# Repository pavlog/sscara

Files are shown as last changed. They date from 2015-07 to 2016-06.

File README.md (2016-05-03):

# sscara
Small size 3d printer with SCARA based mechanics

Current Status: V3 - DONE

V3 Videos:
https://youtu.be/qMoxgC5KaG4
https://youtu.be/IasEUXix5cc
https://youtu.be/JhraS_r1Fzk

History:
* 01.05.2016 - V3 - DONE
* 28.01.2016 - V3 - WIP
* 11.01.2016 - V2 - DONE (fail)
* 05.01.2016 - V2 - Final tests
* 28.07.2015 - V2 - WIP
* 27.07.2015 - V1 - DONE
* 27.04.2015 - V1 - WIP

Precision:
WIP
XY: 0.03 mm with 32 microsteps at 150 mm radius from axes center. (chord length c=2*R*sin(alpha/2), alpha = 1.8/5/32 (stepper/gearratio/nummicrosteps);
Z: GT2 16 teeth pulley with 32 microsteps - 5 μm (http://reprap.org/wiki/Step_rates)
 
Other features:
* Noiseless

Hardware: 
* 4 Nema17 (24mm length shaft)
* Ramps 1.4
* 4 drv8825 (drv8825 is better due to 1/32 microstepping)
* External power supply 5A (without Heated bed)
* Heated bed ????? depends on (but seems like require in 4x time less current than MK2B - because of 4 times lower area)
* 3 small (20x11x7mm) end stoppers
Optional:
* HC-05 bluetooth module (i am happy with it, even firmware flashing done via bluetooth)

Marlin Firmware modifications:
* FIVE_BAR define added for SCARA define
* added M450 - xyz min limits
* added M451 - xyz max limits
* added M452 - xyz home pos
* added M370 X#Angle Y#Angle
* G2/G3 commands support
* Fixed math for pure SCARA (2 arms)

Materials:
* ~1.5 meters(2m max) - GT2 timing belt 6mm(width)
* 3 - GT2 16 teeth pulleys (ID=5mm)
* 4 - Nema17 (24mm shaft length) (39 mm Nema17 might be used for xy)
* 4 - 625 bearings (ID-5mm,OD-16mm,H-5mm)
* 2 - 608 bearings (ID-8mm,OD-22mm,H-7mm)
* 21 - 623 bearings (ID-3mm,OD-10mm,H-4mm)
* 1 - aluminium tube (ID-6mm,OD-8mm) - 350mm max
* 1 - m5 threaded rod - 500mm max
* 1 - m3 threaded rod - 2 meters max
* m3 bolts and nuts
* m5 nuts
* ABS filament to print parts

SCAD:
* use drawArray = [] to draw everything or drawArray=[1,2,3] for parts
* use printLayout to control parts/subparts layout (0 for design, 1 for export) (Some parts need to be rotated to 180 Y) (WIP)
* NemaSize - tweak nema len, NemaLengthMedium,NemaLengthShort,NemaLengthLong

Slicer:
* Slic3r
* ABS - 0.4mm nozzle, setup is described in scad file for each part

Included Software:
* Software/SScaraVisualizer.html (may not be up to date) or use (up to date) https://jsfiddle.net/PavloG/0vq1nf2v/
* Marlin firmware - use https://github.com/pavlog/Marlin (forked from https://github.com/MarlinFirmware/Marlin)

Reachability visualizer
* http://jsfiddle.net/PavloG/0vq1nf2v/

Calibration Guide:
Enable EEPROM in you firmware.

Initial rough calibration:
* G28 goto home
* Steps Per Units - M92 X## Y## where ## is a stepperUnitsPerRevolution*driverMicrostepping*gearboxration/360, (Nema17 1.8deg with drv8825 1/32), v1 = 200*32*5/360 = 88.888, v2 = 142.222

XY init calibration:

* G28 goto home
* M452 X#xx Y#yy - where #xx and #yy is a measured distance from nozzle to the axis center (xx should negative, +/-1 mm is enought)

NOTE: Put your min max software limits a little bit bigger (i used 3 cm)  (use M450 and M451), this is required for the next steps.

XY precise calibration:

Precise Steps Per Units calibration:
* G28 goto home
* M370 X0+#xx Y-90+#yy // move arms to 90 and 180 degrees, #xx and #yy is an extra angle to move arms exactly to 90 and 180 degrees
* M370 X90+#xx Y0+#yy // #xx and #yy from prev step
* if your arms not exacly 0 and 90 degrees use M92 X## Y## +/- values until all sequence above will get 0 and 90 degrees
* Repeat a few times until you get 90 and 180 degrees exactly
* M500 to save data to EEPROM

Precise home offsets calibration:
* G28 goto home
* M370 X0 Y-90 // move arms to 0 and -90 degrees
* M206 X## Y## (where X## Y## is a angular distance to 90 and 180, this is homing offsets in angles, can be used from prev steps)
* Repeat a few times until you get 90 and 180 degrees exactly
* M500 to save data to EEPROM

Z calibration
* G28 Z
* Ajust platform height

Development blog - https://3dgems.blogspot.com

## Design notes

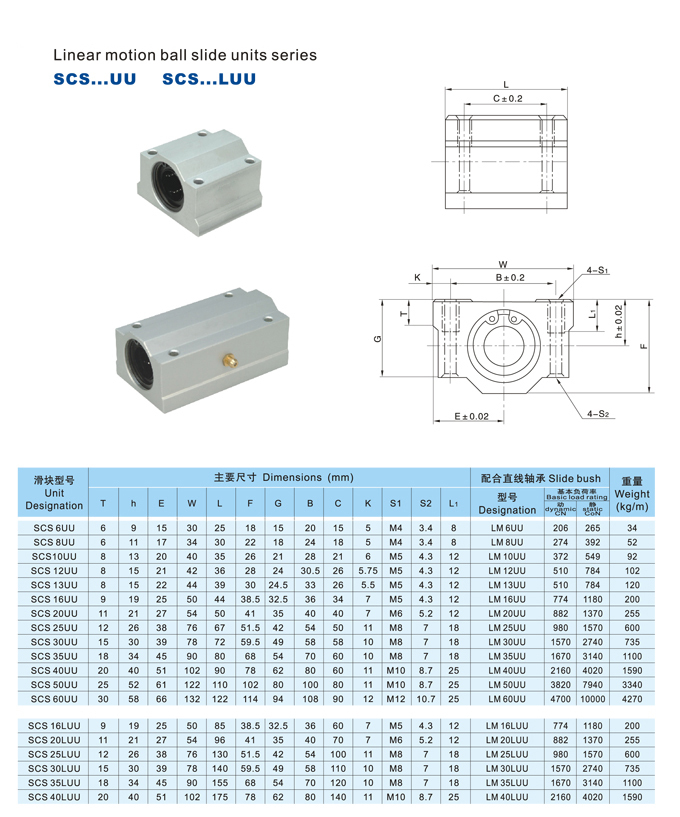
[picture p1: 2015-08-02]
Modules/scs_uu.png

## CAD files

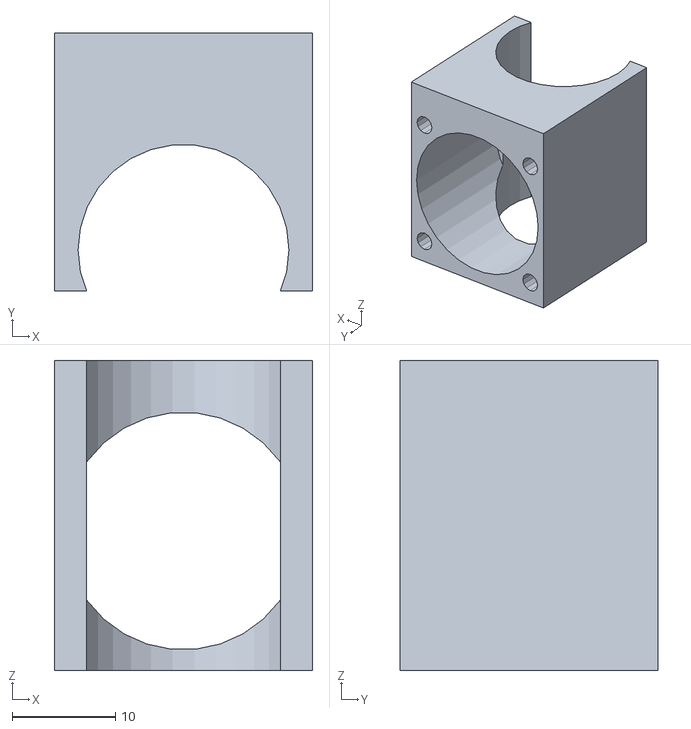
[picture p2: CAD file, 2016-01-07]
Misc/25MMFAN.stl
25.0 x 25.0 x 30.0

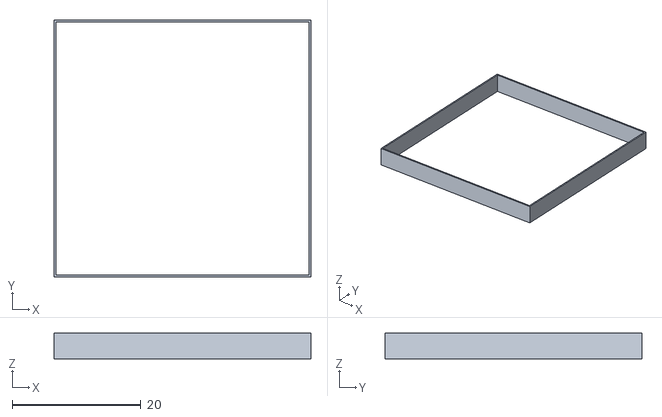
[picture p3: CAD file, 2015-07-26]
STL/CalibrationTests/CalibrationTests40X40.stl
40.0 x 40.0 x 4.00

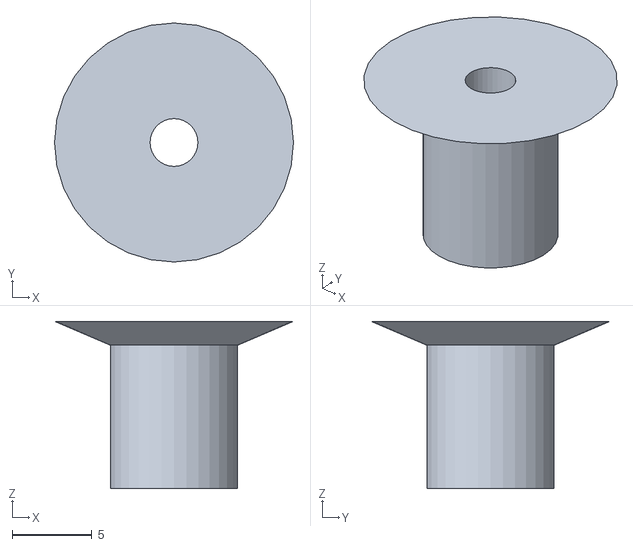
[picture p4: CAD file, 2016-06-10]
STL/V3/part_13_extruder_hinge_stick.stl
15.0 x 15.0 x 10.5

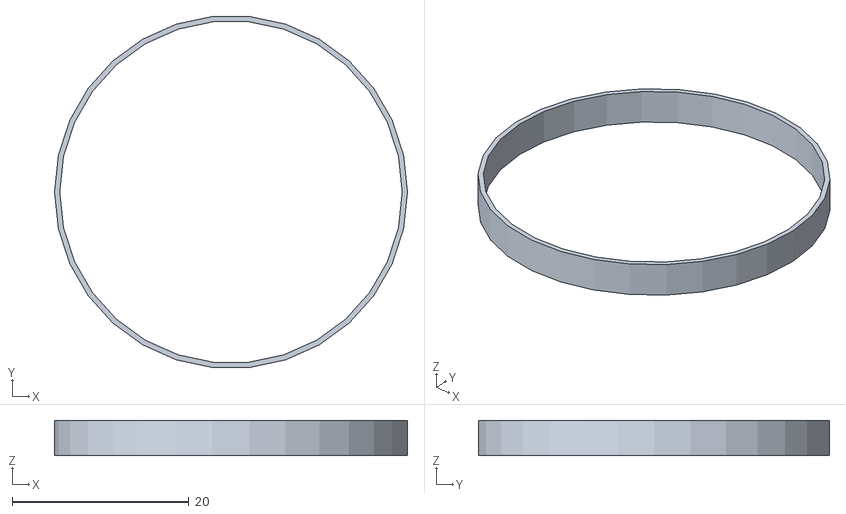
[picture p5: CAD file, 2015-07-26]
STL/CalibrationTests/CalibrationTests_circle.stl
40.0 x 39.8 x 4.00

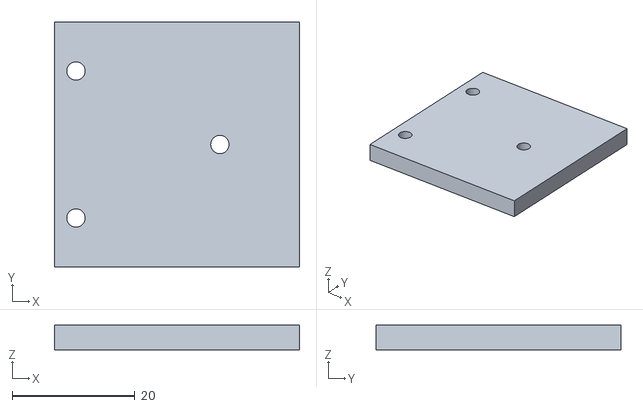
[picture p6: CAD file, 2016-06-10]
STL/V3/part_14_extruder_hinge_plate.stl
40.0 x 40.0 x 4.00

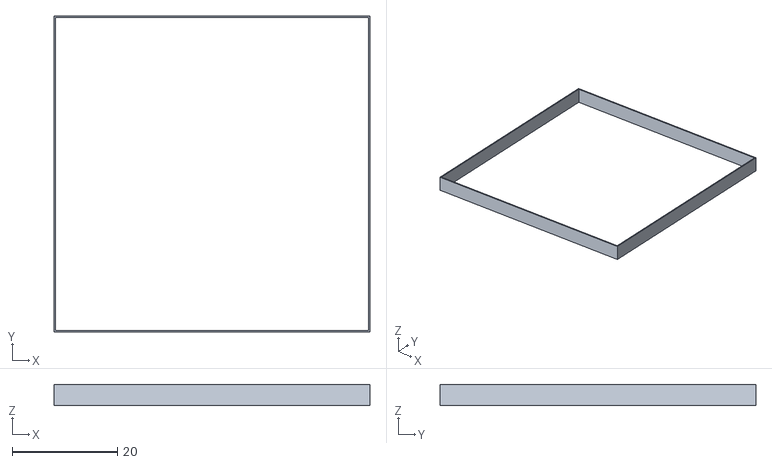
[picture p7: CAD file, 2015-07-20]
STL/CalibrationTests/CalibrationTests60X60.stl
60.0 x 60.0 x 4.00

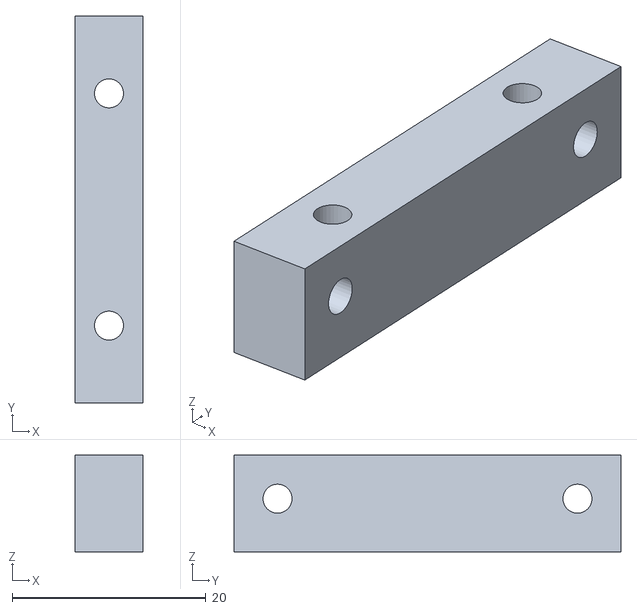
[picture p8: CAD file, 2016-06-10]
STL/V3/part_15_extruder_stepper_mount.stl
7.00 x 40.0 x 10.0

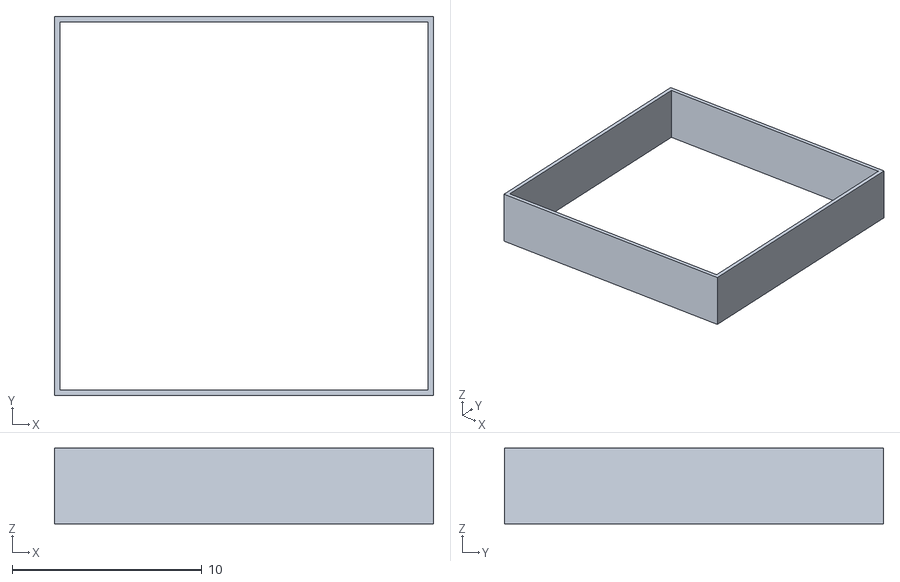
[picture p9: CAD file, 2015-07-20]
STL/CalibrationTests/CalibrationTests.stl
20.0 x 20.0 x 4.00

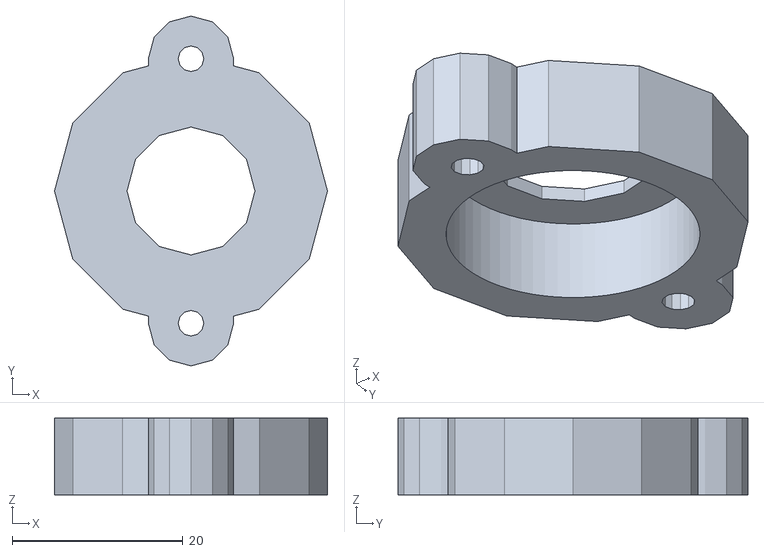
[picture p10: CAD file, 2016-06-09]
STL/V3/part_12_extruder_hinge_mount.stl
32.0 x 41.0 x 9.00

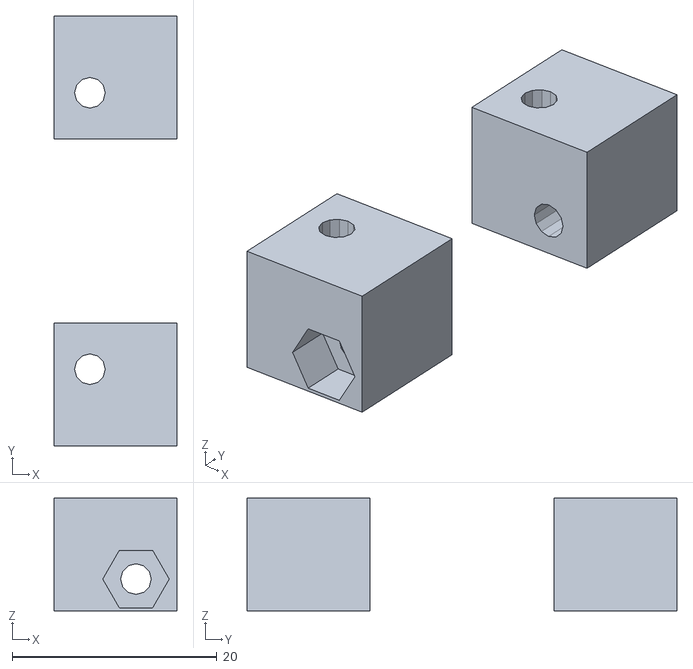
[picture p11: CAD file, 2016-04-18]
STL/V3/topFrontMounts.stl
12.0 x 42.0 x 11.0

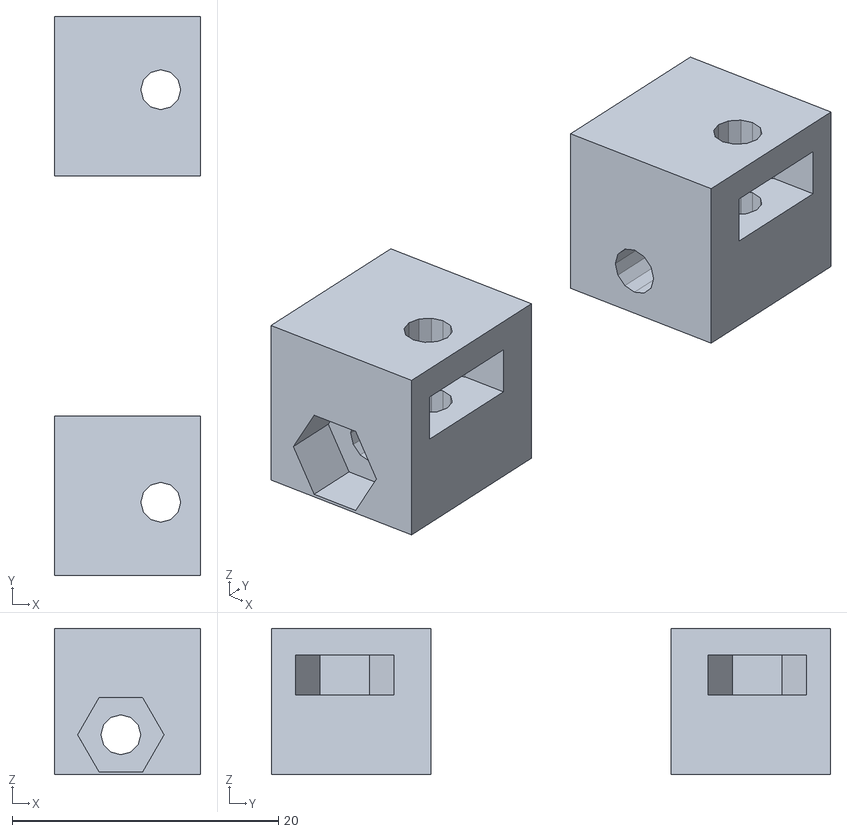
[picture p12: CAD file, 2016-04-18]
STL/V3/topMiddleMounts.stl
11.0 x 42.0 x 11.0

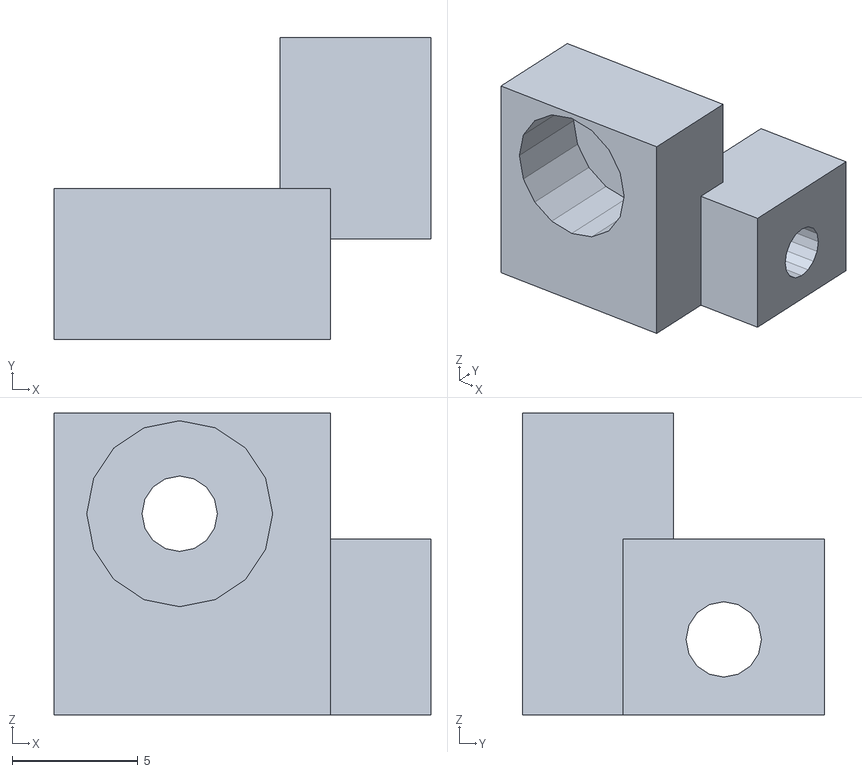
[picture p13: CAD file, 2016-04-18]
STL/V3/part_10_subpart2.stl
15.0 x 12.0 x 12.0

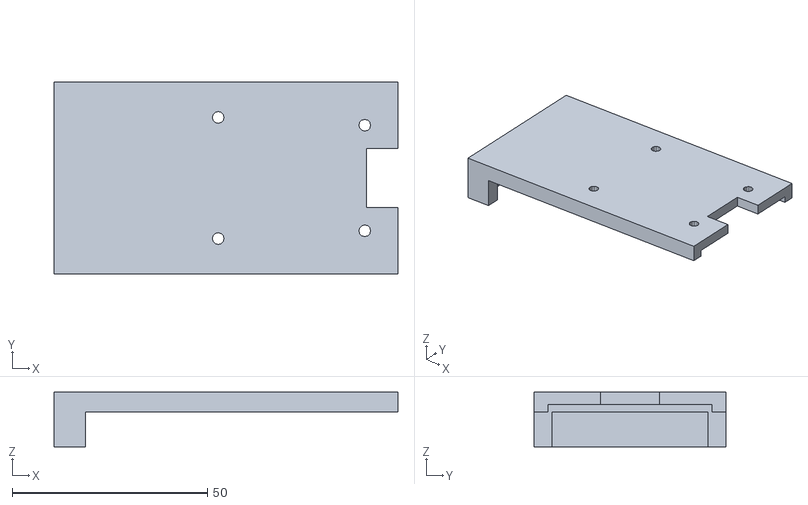
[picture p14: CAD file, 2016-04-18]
STL/V3/topCap.stl
88.0 x 49.0 x 14.0

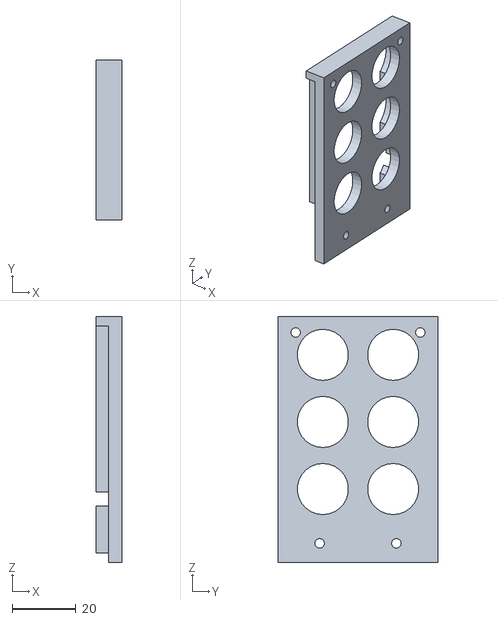
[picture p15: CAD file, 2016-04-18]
STL/V3/part_10_subpart1.stl
8.00 x 50.0 x 77.0

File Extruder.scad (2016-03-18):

// Author: Pavlo Gryb (psg416@gmail.com)

use <Modules/Pulley_T-MXL-XL-HTD-GT2_N-tooth.scad>
use <Modules/ISOThread.scad>
use <Modules/Bearings.scad>
use <Modules/EndStoppers.scad>
use <Modules/Write.scad/Write.scad>
include <Modules/MCAD/stepper.scad>
use <Modules/HotEnds.scad>
use <Modules/LCD.scad>
use <Modules/Misc.scad>
use <Modules/Profiles.scad>
use <Modules/RAMPS.scad>
include <Modules/dimlines.scad>
include <Modules/TextGenerator.scad>

gearRadToTeethEnd = 10.0/2;//7.3/2;// seems like mk8
gearRad = 11.5/2;// semms like mk8
fillamentD = 1.75;
fillamentPenetration = 0.5;//mm
extruderBearingDia = Bearing623Diameter();
extruderBearingH = Bearing623Height();
extruderClearanceH = 0.2;

printLayout = 0;

module ExtruderStepperPanel()
{
					hull()
				{
					translate([-14,-14,0]) cylinder(r=7.2,h=4,$fn=32);
					translate([14,-14,0]) cylinder(r=7.2,h=4,$fn=32);
					translate([14,14,0]) cylinder(r=7.2,h=4,$fn=32);
					translate([-14,14,0]) cylinder(r=7.2,h=4,$fn=32);
					//translate([24.5+extrudeMountZOffset,9,0]) cylinder(r=7.5,h=4);
				}

}

// extruder
//if( drawArray==[] || search(11,drawArray)!=[] )
{
	//printLayout = 1;
	aY = printLayout ? 0 : 90;
	aYY = printLayout ? 180 : -90;
	armX = printLayout ? 12 :0;
	armY = printLayout ? -38 : 0;
	armZ = printLayout ? -24.75 : 0;
	armRZ = printLayout ? 196.69 : 0;
	armRX = printLayout ? 90 : 0;
	armTX = printLayout ? 10 : 0;
	translate ([0,0,0]) rotate([0,aYY,0]) rotate([0,0,aY]) mirror()//rotate([90,0,0]) 
	{
		armH = extruderBearingH+3+3;
		partsOffset = -13;
		if( !printLayout )
		{
			rotate([0,0,90]) Nema17_shaft24_Stepper();
		}
		translate([0,0,-3])
		{
			difference()
			{
				//cube([36,36,4]);
				ExtruderStepperPanel();
				extr = lookup(NemaRoundExtrusionDiameter, Nema17);
				color ("red") translate([0,0,1.5]) cylinder(d=extr+0.5,h=2.5,$fn=32);
				color ("red") translate([0,0,2]) Nema17_shaft24_Stepper(bSrewsOnly=1);
				//extruder mount
				//translate([27,10.5,-30+extrudeMountZOffset]) color("red") rotate([0,0,0]) cylinder(d=3.1,h=50,$fn=16);
				//translate([25.4,3.5,-30+extrudeMountZOffset]) color("red") rotate([0,0,0]) cylinder(d=3.1,h=50,$fn=16);
			}
			difference()
			{
				union()
				{
					color ("red")  translate([gearRadToTeethEnd-1,-12,-armH]) cube([11+3,14,armH]);
					color ("red")  translate([gearRadToTeethEnd+8,-12-1,-armH]) cube([5,3,armH]);
				}
				color( "green") translate([0,-gearRadToTeethEnd-Bearing623Diameter()/2-fillamentD/2,partsOffset+3-2]) cylinder(d=extruderBearingDia+3,h=armH+2);
				color( "green") translate([0,0,partsOffset+3-2]) cylinder(d=gearRad*2+1,h=armH+2);

				// cone
				color( "red") translate([3.9,-gearRadToTeethEnd-fillamentD/2+fillamentPenetration,-armH/2]) rotate([0,90,0]) cylinder(r2=fillamentD/2-0.2,r1=fillamentD/2+1.5,h=2,$fn=16);
				
				// fillamant
				color( "blue") translate([-50,-gearRadToTeethEnd-fillamentD/2+fillamentPenetration,-armH/2]) rotate([0,90,0]) cylinder(d=fillamentD+0.2,h=100,$fn=16);
				color( "blue") translate([10+3,-gearRadToTeethEnd-fillamentD/2+fillamentPenetration,-armH/2]) rotate([0,90,0]) cylinder(d=9,h=100,$fn=16);
				//
			}
			difference()
			{
				union()
				{
					color( "green") hull()
					{
						translate([15.5,-4-gearRadToTeethEnd-Bearing623Diameter()/2-fillamentD/2,partsOffset+3]) cylinder(d=6,h=armH+4);
						translate([20.5,-6-gearRadToTeethEnd-Bearing623Diameter()/2-fillamentD/2,partsOffset+3]) rotate([0,0,25])  cylinder(d=6,h=armH+4,$fn=16);
						translate([15.5,-5.5-gearRadToTeethEnd-Bearing623Diameter()/2-fillamentD/2,partsOffset+3]) cylinder(d=6,h=armH+4);
					}
					//color("blue") translate([25,-4.5-gearRadToTeethEnd-Bearing623Diameter()/2-fillamentD/2,partsOffset+3+4-13]) rotate([0,0,90+70])  cube([5,6.5,23]);
					//color("red") translate([26,-1.8-gearRadToTeethEnd-Bearing623Diameter()/2-fillamentD/2,partsOffset+3+4-13]) rotate([0,0,aY])  cube([5,11,10]);
					color( "green") hull()
					{
						translate([15.5,-4.5-gearRadToTeethEnd-Bearing623Diameter()/2-fillamentD/2,partsOffset+3]) cylinder(d=8,h=armH+4);
						translate([9,-1-gearRadToTeethEnd-Bearing623Diameter()/2-fillamentD/2,partsOffset+3]) cylinder(d=4.5,h=armH+4);
					}
				}
				color ("red") translate([0,0,2]) Nema17_shaft24_Stepper(bSrewsOnly=1);
				//M3 HOLE
				color( "magenta") translate([27,0,-armH/2]) rotate([90,0,0]) rotate([0,-25,0])  cylinder(d=4,h=100,$fn=16);
				color( "magenta") translate([14,-15,-armH/2-10]) rotate([0,90,90+70+180])  cylinder(d=3,h=100,$fn=16);
			}
			difference()
			{
				color ("red")  translate([-gearRadToTeethEnd-15,-12,-armH]) cube([15,14,armH+1]);
				color( "green") translate([0,0,partsOffset+3-2]) cylinder(d=gearRad*2+1,h=armH+2);
				color( "blue") hull()
				{
						translate([0,-gearRadToTeethEnd-Bearing623Diameter()/2-fillamentD/2,partsOffset+3-2]) cylinder(d=extruderBearingDia+3,h=armH+2);
						translate([0,-5-gearRadToTeethEnd-Bearing623Diameter()/2-fillamentD/2,partsOffset+3-2]) cylinder(d=extruderBearingDia+3,h=armH);
						translate([-3,-5-gearRadToTeethEnd-Bearing623Diameter()/2-fillamentD/2,partsOffset+3-2]) cylinder(d=extruderBearingDia+4,h=armH);
				}
				color( "blue") hull()
				{
					 translate([-15.5,-15.5,partsOffset+3-2]) cylinder(d=11+3,h=armH+2);
					 translate([-11.5,-15.5,partsOffset+3-2]) cylinder(d=11+3,h=armH+2);
				}
				// fillamant
				color( "red") translate([-50,-gearRadToTeethEnd-fillamentD/2+fillamentPenetration,-armH/2]) rotate([0,90,0]) cylinder(d=fillamentD+0.2,h=100,$fn=16);
			}
		}
		//#color ("red") translate([0,0,0]) cube([10,10,10]);
		translate([armX,armY,armZ]) rotate([armRX,0,0])  rotate([0,0,armRZ]) translate([0,0,partsOffset])
		{
			difference()
			{
				union()
				{
					color( "green") hull()
					{
						color( "green") translate([-15.5,-15.5,0]) cylinder(d=11+2,h=armH);
						//#color( "green") translate([-12,-gearRadToTeethEnd-Bearing623Diameter()/2-fillamentD/2,0]) cylinder(d=extruderBearingDia+6,h=armH);
					}
					color( "magenta") hull()
					{
						translate([0,-gearRadToTeethEnd-Bearing623Diameter()/2-fillamentD/2,0]) cylinder(d=extruderBearingDia+2,h=armH);
						translate([0,-5-gearRadToTeethEnd-Bearing623Diameter()/2-fillamentD/2,0]) cylinder(d=extruderBearingDia+3,h=armH);
						translate([-3,-5-gearRadToTeethEnd-Bearing623Diameter()/2-fillamentD/2,0]) cylinder(d=extruderBearingDia+3,h=armH);
					}
					color( "green") hull()
					{
						translate([-15.5,-15.5,0]) cylinder(d=11+2,h=armH);
						translate([15,-27,0]) rotate([0,0,23]) cylinder(d=11,h=armH,$fn=4);
					}
				}
				// bearing hole
				color( "silver")hull()
				{
					translate([0,-gearRadToTeethEnd-Bearing623Diameter()/2-fillamentD/2,(armH-Bearing623Height())/2-extruderClearanceH]) cylinder(r=Bearing623Diameter()/2+1.5,h=Bearing623Height()+extruderClearanceH*2,$fn=32);
					translate([0,10-gearRadToTeethEnd-Bearing623Diameter()/2-fillamentD/2,(armH-Bearing623Height())/2-extruderClearanceH]) cylinder(r=Bearing623Diameter()/2+1.5,h=Bearing623Height()+extruderClearanceH*2,$fn=32);
				}
				// fillamant hole
				color( "blue") translate([-50,-gearRadToTeethEnd-fillamentD/2+fillamentPenetration,armH/2]) rotate([0,90,0]) cylinder(d=fillamentD+0.2,h=100,$fn=16);
				// bearing shaft
				color( "silver") translate([0,-gearRadToTeethEnd-Bearing623Diameter()/2-fillamentD/2,-5]) cylinder(d=3.1,h=20,$fn=16);
				//
				color( "silver") hull()
				{
					translate([0,-gearRadToTeethEnd-Bearing623Diameter()/2-fillamentD/2,(armH-Bearing623Height())/2-0.5-0.1]) cylinder(d=8,h=0.5,$fn=16);
					translate([0,10-gearRadToTeethEnd-Bearing623Diameter()/2-fillamentD/2,(armH-Bearing623Height())/2-0.5-0.1]) cylinder(d=8,h=0.5,$fn=16);
				}
				//
				color( "silver") hull()
			{
				translate([0,-gearRadToTeethEnd-Bearing623Diameter()/2-fillamentD/2,(armH-Bearing623Height())/2+Bearing623Height()+0.1]) cylinder(d=8,h=0.5,$fn=16);
				translate([0,10-gearRadToTeethEnd-Bearing623Diameter()/2-fillamentD/2,(armH-Bearing623Height())/2+Bearing623Height()+0.1]) cylinder(d=8,h=0.5,$fn=16);
			}
				color( "silver") translate([-15.5,-15.5,-5]) cylinder(d=3.05,h=40,$fn=16);
			// gear hole
			color( "green") translate([0,0,-1]) cylinder(d=gearRad*2+1,h=armH+2);
			// M3 HOLE
			color( "blue") translate([27,0,armH/2]) rotate([90,0,0]) rotate([0,-25,0])  cylinder(d=4,h=100,$fn=16);
			//color( "blue") translate([27,0,armH/2]) rotate([90,0,0]) rotate([0,-25,0])  cylinder(d=4,h=100,$fn=16);
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

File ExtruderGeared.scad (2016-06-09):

// Author: Pavlo Gryb (psg416@gmail.com)

use <Modules/Pulley_T-MXL-XL-HTD-GT2_N-tooth.scad>
use <Modules/ISOThread.scad>
use <Modules/Bearings.scad>
use <Modules/EndStoppers.scad>
use <Modules/Write.scad/Write.scad>
include <Modules/MCAD/stepper.scad>
use <Modules/HotEnds.scad>
use <Modules/LCD.scad>
use <Modules/Misc.scad>
use <Modules/Profiles.scad>
include <Modules/dimlines.scad>
include <Modules/TextGenerator.scad>
use <ExtruderGearsHelical.scad>


gap = 29.884; //distance between centres of gears 
height = 10;
bPrint = 1;
partIndex = -1;

module Gear()
{
		cylinder(d=8.5,h=11,$fn=32);
		cylinder(d=10,h=7,$fn=32);
}

module ExtruderStepperPanel(h=4)
{
	hull()
	{
		translate([-14,-14,0]) cylinder(r=7,h=h);
		translate([14,-14,0]) cylinder(r=7,h=h);
		translate([14,14,0]) cylinder(r=7,h=h);
		translate([-14,14,0]) cylinder(r=7,h=h);
		//translate([24.5+extrudeMountZOffset,9,0]) cylinder(r=7.5,h=4);
	}

}

module GearedExtruder(partIndex)
{
	if( partIndex==-1 || partIndex==5 )
	{
		translate([10+6,0,gap]) rotate([0,-90,0]) difference() 
		{
			if( bPrint==1 )
			{
				bigGear();
			}
			else
			{
				translate([0,0,-5]) cylinder(d=42,h=10,$fn=32);
			}
				
			translate([0,0,-10]) cylinder(d=5,h=20,$fn=32);
			difference() 
			{  //top bevel
				cylinder(30,30,0);
				cylinder(28,28,0);
			}
			mirror([0,0,180]) 
			translate([0,0,0]) 
			difference() 
			{ //bottom bevel
				cylinder(30,30,0);
				cylinder(28,28,0);
			}
		}
	}

	if( partIndex==-1 || partIndex==4 )
	{
		shaft5dia = 5.5;
		translate([10+6,0,0]) rotate([0,-90,0]) difference() 
		{
			union() 
			{
				if( bPrint )
				{
					translate([0,0,0]) rotate([180,0,0])
					{
							smallGear();
							translate([0,0,-height/2-2]) cylinder(d=shaft5dia,h=height+2,$fn=32);
					}
				}
				else
				{
					translate([0,0,-5]) cylinder(d=15,h=10,$fn=32);
				}
				//offset = -10;
				difference() 
				{
					union()
					{
						translate([0,0,+1]) difference()
						{
							rotate([180,0,3.8]) smallGear();
							translate([0,0,-height/2-0.1]) cylinder(d=20,h=9,$fn=32);
							translate([0,0,-height/2-1]) cylinder(d=shaft5dia,h=height+2,$fn=32);
						}

						//translate([0,0,-height/2-1]) cylinder(d=11,h=1,$fn=32);
						translate([0,0,-height/2+11]) cylinder(d=18,h=9,$fn=32);
					}
					hull()
					{
						translate([-4,0,height/2+5]) rotate([0,-90,0]) cylinder(d=7,h=2.7,$fn=6);
						translate([-4,0,height/2+5+20]) rotate([0,-90,0]) cylinder(d=7,h=2.7,$fn=6);
					}
					translate([0,0,height/2+5]) rotate([0,-90,0]) cylinder(d=3,h=20,$fn=24);
				}
			}
			difference()
			{
				translate([0,0,-20]) cylinder(d=shaft5dia,h=40,$fn=32);
				translate([0-3,-3,-10 ]) cube([.8,6,height+20]); //hole flat
			}
			
			//top bevel
			//translate([0,0,0]) difference() 
			//{  
	//			cylinder(14,14,0);
				//cylinder(12.8,12.8,0);
			//}

			//top bevel
			mirror([0,0,180]) translate([0,0,0]) difference() 
			{ 
				cylinder(14,14,0);
				cylinder(12.8,12.8,0);
			}
		}
	}

	translate([10,0,gap]) rotate([0,-90,0]) 
	{
			if( partIndex==-1 )
			{
				color("silver") translate([0,0,2]) cylinder(d=rolson_hex_nut_dia(5),h=rolson_hex_nut_hi(5),$fn=6);

				color("green") translate([0,0,-15]) cylinder(d=5,h=50,$fn=32);
				color("silver") translate([0,0,6]) Bearing625();
				color("gold") translate([0,0,16]) Gear();
				color("silver") translate([0,0,27]) Bearing625();
			}
		
			if( partIndex==-1 || partIndex==1 )
			{
				difference()
				{
					color("green") hull()
					{
							translate([-8.8,-15,5]) cube([2,30,6]);
							translate([4,0,5]) cylinder(d=20,h=6,$fn=32);
							color("silver") translate([12,8,5]) cylinder(d=6,h=6,$fn=32);
							color("silver") translate([12,-8,5]) cylinder(d=6,h=6,$fn=32);
					}
					color("silver") translate([0,0,5]) cylinder(d=13,h=10,$fn=32);
					color("silver") translate([0,0,6]) cylinder(d=17,h=10,$fn=32);
					color("silver") translate([-5,10,0]) cylinder(d=3,h=40,$fn=32);
					color("silver") translate([-5,-10,0]) cylinder(d=3,h=40,$fn=32);
					color("silver") translate([12,8,0]) cylinder(d=3,h=40,$fn=32);
					color("silver") translate([12,-8,0]) cylinder(d=3,h=40,$fn=32);
				}
			}
			
			if( partIndex==-1 || partIndex==2 )
			{
				color("magenta") translate([0,0,5]) difference()
				{
						difference()
						{
								union()
								{
				color("blue") hull()
				{
						translate([-8.8,-15,6]) cube([2,30,11+5]);
						translate([4,0,6]) cylinder(d=20,h=11+5,$fn=32);
						color("silver") translate([12,8,6]) cylinder(d=6,h=11+5,$fn=32);
						color("silver") translate([12,-8,6]) cylinder(d=6,h=11+5,$fn=32);
				}
				 //translate([5,0,9+5]) rotate([90,0,0]) cylinder(d=16,h=7.1+5+1,$fn=32);
				 translate([-3,0,6]) rotate([90,0,0]) cube([16,16,13]);
				hull()
				{
					translate([10,-5,6]) rotate([90,0,0]) cube([4.9,16,8]);
					//translate([15+1,-12-1,6]) rotate([90,0,-60]) cube([4,16,2]);
					//#translate([15,-12,6]) rotate([90,0,0]) cube([4,16,2]);
					translate([15+1,-12-1,6]) rotate([0,0,0]) cylinder(r=3,h=16,$fn=32);//([4,16,2]);
				}
				//translate([14.5,-13.5,9.0+5]) rotate([-90,0,-44]) cylinder(d=7,h=5,$fn=16);
			}

						//translate([5,-15,6+5]) cube([20,20,11]);
						//translate([7,-15,6+5]) cube([20,20,11]);
					difference()
			{
						hull()
						{
										translate([5,0,6]) cylinder(d=10,h=11.2+5);
										translate([15,0,6]) cylinder(d=11,h=11.2+5);
						}
						//translate([10,0,12]) rotate([0,0,0]) cylinder(d=11,h=20+1,$fn=32);
						difference()
						{
						color("silver") translate([5,-6,6]) rotate([0,0,45]) cylinder(d=5,h=20+1,$fn=32);
						translate([10,0,6]) rotate([0,0,0])  cylinder(d=11.5,h=20+1,$fn=32);
						}
					}
						color("silver") translate([12,8,6-0.1]) cylinder(d=10,h=11.2+5,$fn=32);
				}
				
				// fillamant
				#translate([5,20,9.0+5]) rotate([90,0,0]) cylinder(d=1.75,h=50,$fn=16);
				
				#translate([5,-3.5,9.0+5]) rotate([90,0,0]) cylinder(r1=4/2,r2=1.75/2,h=2,$fn=16);

				 translate([5,-8,9+5]) rotate([90,0,0]) cylinder(d=9,h=5,$fn=32);
				 translate([-3,-13,6-0.1]) rotate([90,0,0]) cube([15,16.2,20]);
				 translate([-3,-15.5,0]) scale([1,1,1]) cylinder(d=5,h=40,$fn=32);
				 translate([12,-15.5,0]) scale([1,1,1]) cylinder(d=5,h=40,$fn=32);
				 //#translate([5,-13,9+5]) rotate([90,0,0]) cylinder(d=16,h=7+2,$fn=32);

				//color("silver") translate([0,0,6-0.1]) cylinder(d=16.2,h=5+1.2,$fn=32);
		//		difference()
				{
					color("silver") translate([0,0,6-0.1]) cylinder(d=12,h=20+1,$fn=32);
						translate([10,0,6]) rotate([0,0,0])  cylinder(d=11.5,h=20+1,$fn=32);
				}
				color("silver") translate([-5,10,0]) cylinder(d=3,h=40,$fn=32);
				color("silver") translate([-5,-10,0]) cylinder(d=3,h=40,$fn=32);
				color("silver") translate([12,8,0]) cylinder(d=3,h=40,$fn=32);
				color("silver") translate([12,-8,0]) cylinder(d=3,h=40,$fn=32);

				//color("silver") translate([0,0,6+5]) cylinder(d=9.2,h=11+1,$fn=32);
				#translate([10,0,12]) rotate([0,0,0]) Bearing623();
				#color("silver") translate([0,0,6-0.1]) cylinder(d=10,h=20+1,$fn=32);

			hull()
			{
				translate([12-1,-15.5,9.0+5]) rotate([-90,0,-44]) cylinder(d=3,h=50,$fn=16);
			 //translate([12,-15.5,9.0+5]) rotate([-90,0,-50]) cylinder(d=3,h=50,$fn=16);
			}
				}
				//   color("red") 
		//    difference()
				//{
						//translate([5,-3,19]) rotate([90,0,0]) cylinder(d=16.5,h=17,$fn=32);
						//translate([5,-13,19]) rotate([90,0,0]) cylinder(d=10,h=7.1,$fn=16);
				//}

			}

			if( partIndex==-1 || partIndex==3 )
			{

			translate([0,0,21]) difference()
			{
			color("green") hull()
			{
					translate([-8.8,-15,6]) cube([2,30,5]);
					translate([4,0,6]) cylinder(d=20,h=5,$fn=32);
					color("silver") translate([12,8,6]) cylinder(d=6,h=5,$fn=32);
					color("silver") translate([12,-8,6]) cylinder(d=6,h=5,$fn=32);
			}
			color("silver") translate([0,0,6]) cylinder(d=16.2,h=10,$fn=32);
			color("silver") translate([-5,10,0]) cylinder(d=3,h=40,$fn=32);
			color("silver") translate([-5,-10,0]) cylinder(d=3,h=40,$fn=32);
			color("silver") translate([12,8,0]) cylinder(d=3,h=40,$fn=32);
			color("silver") translate([12,-8,0]) cylinder(d=3,h=40,$fn=32);
			}
			//hull()
			{
			 //   color("blue") translate([-8.8,-15,6]) cube([5,30,10]);
			}
			}

			if( partIndex==-1 || partIndex==6 )//|| partIndex==2 )
			{

			difference()
			{
			union()
			{
			hull()
			{
				color("silver") translate([12,8,6+5]) cylinder(d=8,h=11+5,$fn=32);
				color("silver") translate([12,8-8,6+5]) cylinder(d=8,h=11+5,$fn=32);
			}
			hull()
			{
				color("silver") translate([12,8-8.5,6+5]) cylinder(d=8,h=11+5,$fn=32);
				color("silver") translate([12-2,8-8,6+5]) cylinder(d=10,h=11+5,$fn=32);
			}
			hull()
			{
				color("silver") translate([12,8,6+5]) cylinder(d=8,h=11+5,$fn=32);
				#color("silver") translate([12+9+2,8-18,6+5]) cylinder(d=6,h=11+5,$fn=32);
			}
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

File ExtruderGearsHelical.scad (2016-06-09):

$fn=200;
include <MCAD/involute_gears.scad>; 
include <MCAD/regular_shapes.scad>;

gap = 29.884; //distance between centres of gears 
height=10;

module bigGear(
	pressure_angle=30,
	twist=200,
	dia = 45.3,
	teeth=34,
	circles=6) 
{
pitch =dia / (teeth /180);

//Big Gear
gear (number_of_teeth=teeth,
	circular_pitch=pitch,
	pressure_angle=pressure_angle,
	clearance = 0.2,
	gear_thickness = height/2*0.5,
	rim_thickness = height/2,
	rim_width = 1,
	hub_thickness = 5,
	hub_diameter=12,
	bore_diameter=5,
	circles=circles,
	twist=twist/teeth,
	circle_facets=3,
	involute_facets=6);
	
mirror([0,0,1])
gear (number_of_teeth=teeth,
	circular_pitch=pitch,
	pressure_angle=pressure_angle,
	clearance = 0.2,
	gear_thickness = height/2, //flat bottom
	rim_thickness = height/2,
	rim_width = 1,
	hub_thickness = 4,
	hub_diameter=12,
	bore_diameter=3,
	circles=circles,
	twist=twist/teeth,
	circle_facets=3,
	involute_facets=6);
}

module smallGear(
	pressure_angle=30,
	twist=200,
	dia = 14.4,
	teeth=11,
	circles=6) 
{
pitch =dia / (teeth /180);

//Small Gear
gear (number_of_teeth=teeth,
	circular_pitch=pitch,
	pressure_angle=pressure_angle,
	clearance = 0.2,
	gear_thickness = height/2,
	rim_thickness = height/2,
	rim_width = 1,
	hub_thickness = 4,
	hub_diameter=10,
	bore_diameter=5.2,
	circles=circles,
	twist=twist/teeth,
	circle_facets=3,
	involute_facets=6);
	
mirror([0,0,1])
gear (number_of_teeth=teeth,
	circular_pitch=pitch,
	pressure_angle=pressure_angle,
	clearance = 0.2,
	gear_thickness = height/2, //flat bottom
	rim_thickness = height/2,
	rim_width = 1,
	hub_thickness = 4,
	hub_diameter=10,
	bore_diameter=5.2,
	circles=circles,
	twist=twist/teeth,
	circle_facets=3,
	involute_facets=6);
}


difference() {
	bigGear();
	translate([0,0, (height/2)-5.1]) hexagon_prism(5.2,3.1); //Nut Trap hole
	translate([0,0, -(height/2)-0.1]) hexagon_prism(5.2,1.7); //thread hole
	difference() {  //top bevel
		cylinder(30,30,0);
		cylinder(28,28,0);
	}
	mirror([0,0,180]) 
	difference() { //bottom bevel
		cylinder(30,30,0);
		cylinder(28,28,0);
	}
	
}


difference() {
	union() {
		translate([gap,0,0]) rotate([180,0,0])	smallGear();
		translate([gap-3,-3,-(height/2) ]) cube([.8,6,height]); //hole flat
	}
	translate([gap,0,0]) 
	difference() {  //top bevel
		cylinder(14,14,0);
		cylinder(12.8,12.8,0);
	}
	mirror([0,0,180]) 
	translate([gap,0,0]) 
	difference() {  //top bevel
		cylinder(14,14,0);
		cylinder(12.8,12.8,0);
	}
}

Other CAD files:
STL/V3/part_10_subpart3.stl
STL/V3/part_07_zmin_rails.stl
STL/V3/part_07_zmin_body.stl
STL/V3/part_09_endstoper_bottomarm.stl
sscaraV3.scad
Misc/CalibrationTests.scad
Modules/Bearings.scad
Modules/Belt_Generator.scad
Modules/EndStoppers.scad
Modules/HotEnds.scad
Modules/ISOThread.scad
Modules/LCD.scad
Modules/Misc.scad
Modules/Profiles.scad
Modules/Pulley_T-MXL-XL-HTD-GT2_N-tooth.scad
Modules/RAMPS.scad
Modules/TextGenerator.scad
Modules/dimlines.scad
STL/V1/part_10_zstepper_mount.stl
STL/V1/part_13_belt_coupler.stl
STL/V1/part_14_xyendstoppers_spacer.stl
STL/V1/part_17_ramps_bottom_spacers.stl
STL/V1/part_18_ramps_bottom_mount.stl
STL/V1/part_19_ramps_middle_spacers.stl
STL/V1/part_1_pulley_bottom.stl
STL/V1/part_20_ramps_top_mount.stl
STL/V1/part_21_upper_bearing_fixator.stl
STL/V1/part_22_upper_bearing_mount.stl
STL/V1/part_23_extruder_parts.stl
STL/V1/part_24_axis_bottom_arm.stl
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

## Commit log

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2015-06-04 !N endstopper module (now only 20x11)
    [EndStoppers.scad]
2015-06-04 !U Pulleys EndStoppers arms + outertube holder
    [Bearings.scad, EndStoppers.scad, Nano.scad]
2015-06-04 !U explode mode fixed
    [Nano.scad]
2015-06-05 !U top pulley fix
    [Nano.scad]
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2015-06-06 !U pulleys fixed (test printer of all 3 parts done)
    [Nano.scad, pulley_bottom.stl, pulley_top.stl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]
2015-06-06 !U 608 bearing and steppers preparation
    [Bearings.scad, Nano.scad]
2015-06-07 !U rods support and first 608 bearing support
    [Nano.scad, Pulley_T-MXL-XL-HTD-GT2_N-tooth.scad]
2015-06-08 !U formatting and extra mount added to right side
    [Nano.scad]
2015-06-08 !U mount holes added to base, readme updated
    [Nano.scad]
2015-06-08 !N ramps 1.4 with steppers and heat sinks stl model added
    [Nano.scad]
2015-06-08 !U end stoppers mount, z max end stopper
    [EndStoppers.scad, Nano.scad]
2015-06-09 !U xy supports added
    [Nano.scad]
2015-06-09 !U XYZ steppers bases + bottoms
    [Nano.scad]
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2015-06-10 !U bases modifications and more strength for z axis stepper
    [Nano.scad]
2015-06-10 !U z axis stepper support updated
    [Nano.scad]
2015-06-10 !U XY steppers mounts exported
    [part_7_xstepper_mount.stl, part_8_ystepper_mount.stl]
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2015-06-11 !U part 4 exported
    [Nano.scad, part_4_pulleys_base.stl]
2015-06-12 !U bearings fixer, and part 13
    [Nano.scad]
2015-06-13 !U a few fixes (appeared after first prints), still exports
    [Nano.scad, part_10_zstepper_mount.stl, part_5_pulleys_bearing_mount.stl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]
2015-06-14 !U 13 parts printed and checked
    [Nano.scad, part_11_bases_clamp.stl, part_12_bases_clamp.stl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]
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2015-06-15 !U explode mode updated, bearings added to show their places
    [Nano.scad]
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2015-06-16 !U extra holes (for fan mount)
    [Nano.scad]
2015-06-16 !U more parts added (ramps 1.4 mounts)
    [Nano.scad]
2015-06-16 !U ramps 1.4 printed (a few problems solved)
    [Nano.scad, part_15_pulleys_zstepper_coupler.stl, part_16_pulleys_zstepper_coupler.stl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]
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2015-06-18 !U extruder and top bearing mount
    [Bearings.scad, Nano.scad]
2015-06-18 !u more parts printed and fixed
    [Nano.scad, part_21_upper_bearing_fixator.stl, part_22_upper_bearing_mount.stl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]
2015-06-18 !U top bearing mount platform fixes
    [Nano.scad, part_22_upper_bearing_mount.stl]
2015-06-19 !U some parts renamed
    [part_1_pulley_bottom.stl, part_2_pulley_top.stl, part_3_pulley_top_fixator.stl]
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2015-06-19 !U arms parts updated
    [Nano.scad]
2015-06-19 !U arms and nozzle added
    [Nano.scad]
2015-06-22 !U belt coupler revised
    [Belt_Generator.scad, Nano.scad, part_13_belt_coupler.stl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]
2015-06-22 !U arms updated and ready for printing
    [Nano.scad]
2015-06-22 !U axis arms exported and printed
    [part_24_axis_bottom_arm.stl, part_26_axis_top_arm.stl]
2015-06-23 !U end effectors arms
    [Bearings.scad, Nano.scad]
2015-06-23 !U end effectors arm updated and exported
    [Nano.scad, part_25_arm1.stl, part_27_arm2.stl]
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2015-06-24 !U z platform added (WIP)
    [Nano.scad]
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2015-06-26 !U outer carret part
    [Nano.scad]
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2015-06-28 !U a lot of fixes
    [Belt_Generator.scad, Nano.scad, part_18_ramps_bottom_mount.stl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]
2015-06-29 !U extra holes for some parts
    [Nano.scad, part_18_ramps_bottom_mount.stl, part_20_ramps_top_mount.stl]
2015-06-30 !U lcd 2004 panel mount
    [Nano.scad, part_12_bases_clamp.stl, part_34_lcd_2004_mount.stl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]
2015-06-30 !U lcd holes fixed
    [Nano.scad, part_34_lcd_2004_mount.stl]
2015-07-01 !U code review and small refactor
    [Nano.scad]
2015-07-02 !U bed structural elements
    [Nano.scad, part_35_bed_supports.stl]
2015-07-03 !U holes changed in carret
    [Nano.scad, part_33_carret_outer.stl]
2015-07-06 !B more papers printed, math update
    [Nano.scad, part_36_case_lower_back.stl]
2015-07-06 !U cables holder added
    [Nano.scad, part_37_arms_cable_holders.stl]
2015-07-06 !U calibration plate added
    [Nano.scad, part_38_calibration_plate.stl]
2015-07-06 !U part 37 removed (cable holders) 37 is vacant index, calibration plate decreased in size
    [Nano.scad, part_37_arms_cable_holders.stl, part_38_calibration_plate.stl]
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2015-07-09 !U f512m bearing added, belt tensioner added, readme updated
    [Bearings.scad, Nano.scad, part_24_axis_bottom_arm.stl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]
2015-07-09 !U extruder experiments, need to be improved
    [Nano.scad, part_23_extruder_parts.stl]
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2015-07-12 !U base case parts
    [Nano.scad, part_37_case_lower_front.stl]
2015-07-13 !U base case and print bed updated to match each other, step per unit calibration guide
    [Nano.scad, part_37_case_lower_front.stl]
2015-07-13 !U part 37 minor fixes
    [Nano.scad, part_37_case_lower_front.stl]
2015-07-15 !U calibration test, code cleanup
    [CalibrationTests.scad, CalibrationTests.stl, Nano.scad]
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2015-07-20 !U hot end mount extra arm
    [CalibrationTests.stl, CalibrationTests60X60.stl, part_24_axis_bottom_arm.stl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]
2015-07-22 !U arms redesigned a little bit
    [CalibrationTests.scad, CalibrationTests.stl, part_11_bases_clamp.stl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]
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2015-07-27 !U hotend moved to extrnal file, v2 placeholder
    [CalibrationTests.stl, HotEnds.scad, sscara.scad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]
2015-07-27 !U hot end cleanup
    [sscara.scad]
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2015-07-28 !R lcd moved to lcd module file
    [LCD.scad, sscara.scad]
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2015-07-29 !U scara v2 and experements
    [experiments.scad, sscaraV2.scad]
2015-07-30 !U v2 first parts
    [sscaraV2.scad]
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2015-08-01 !U 2 gear pulleys redesigned for v2. Refactor and code cleanup
    [EndStoppers.scad, part_1_pulley_bottom.stl, part_2_pulley_top.stl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]
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2015-08-03 !U part3 redesigned
    [sscaraV2.scad]
2015-08-03 !U v1 part3 moved to v1 folder
    [part_3_pulley_top_fixator.stl]
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2015-08-04 !U part 5 redesign
    [Misc.scad, sscaraV2.scad]
2015-08-05 !U STL files sorting
    [CalibrationTests.stl, CalibrationTests40X40.stl, CalibrationTests60X60.stl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]
2015-08-05 !U updated part4, part5 - WIP
    [cnc.scad, sscaraV2.scad]
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2015-08-08 !U parts 5,6,7 progress
    [sscaraV2.scad]
2015-08-09 !U v2 changes, part9
    [CalibrationTests.scad, LCD.scad, sscaraV2.scad]
2015-08-10 !U extruder place research
    [sscaraV2.scad]
2015-08-10 !U part 12 and extruder
    [sscaraV2.scad]
2015-08-10 !U ramps x pos paramerized
    [sscaraV2.scad]
2015-08-11 !U extruder mount holes
    [cnc.scad, sscaraV2.scad]
2015-08-11 !U a lot of changes
    [sscaraV2.scad]
2015-08-12 !U z stepper mount, z axis
    [sscaraV2.scad]
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2015-12-08 !B spacers z fixed
    [sscaraV2.scad]
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2016-01-25 !U lcd module - size fixed
    [LCD.scad]
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
